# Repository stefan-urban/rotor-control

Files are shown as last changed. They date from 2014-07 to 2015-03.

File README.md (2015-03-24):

Rotor control with BeagleBone Black
===================================

Dieses Projekt entstand als Teil meiner Bachelorarbeit. Es zielt darauf ab ein Interface für zwei Antennenrotoren (unterschiedlicher Hersteller) zu bauen. Dieses soll eine Schnittstelle zu hamlib besitzen.



Vorraussetzungen
----------------

Hardware
- BeagleBone Black (=BBB)
- Cape wie unter dem Ordner `/hardware/eagle-project`
- Rotoren:
 - Create ERC5A (Elevation)
 - Yaesu G-2800DXC (Azimuth)

Software
- Debian 7.x mit
 - libpcre3-dev
 - libconfig-dev
 - libhamlib-utils (beinhaltet rotctl, rotctld)
- Auf dem Host-PC
 - Gpredict

Installation & Inbetriebnahme
-----------------------------

1. Software (unter `/software/`) aus diesem Repository in beliebigen Ordner auf dem BBB speichern.

2. (Optional) Konfigurationsfile unter `/etc/rotor_control.conf` anlegen. Eine Beispielkonfiguration ist im Ornder `docs` beigelegt.

3. (Optional) Rsyslogd konfigurieren.

 Standardmäßig werden alle Logging-Meldungen in `/var/log/syslog` mit allen anderen Meldungen vom System vermischt. Wie unser Programm ein eigene Logging-Datei erhält wird im beiliegenen Dokument [syslog.md](docs/syslog.md) erklärt.

5. Installieren
 ```
 debian@beaglebone:~/code/rotor-control/software$ sudo ./scripts/install.sh
 ```

 Jetzt werden alle erforderlichen Dateien in die entsprechenden Verzeichnise kopiert:
 - Programm und Start/Stop-Skripte nach `/opt/rotor-control/`
 - Daemon nach `/etc/init.d/`

6. Dienst starten
 ```
 debian@beaglebone:~/code/rotor-control/software$ sudo service rotor-control start
 ```

8. Verbindung mit gPredict aufbauen

 8.1. Gpredict starten
 
 8.2. Unter _Bearbeiten_ > _Einstellungen_ > _Interfaces_ > _Rotators_ einen neuen Rotor hinzufügen.
 
 8.3 Im Hauptfenster rechts oben auf den nach unten zeigenden Pfeil drücken und im erscheinenen Menü _Antennenkontrolle_ auswählen
 
 8.4 Es erscheint folgendes Fenster:

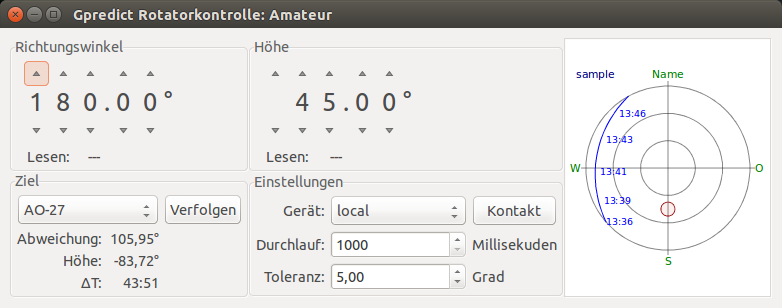
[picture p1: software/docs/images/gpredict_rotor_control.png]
gpredict_rotor_control
 
 
 8.5 Mit Drücken von _Kontakt_ wird die Verbindung zum BBB hergestellt und versucht die eingestellt Position anzufahren.

Verwendung ohne Rotoren
-----------------------

Zum Debugging ist es oft hilfreich das Programm __ohne__ die Rotorenanbindung zu betreiben. Dies ist möglich wenn in der Konfiguration die Simulation eingeschaltet wird. Dann wie oben beschrieben vorgehen.

Hintergrund: Als Rotorenansteuerung kommen jetzt nicht diverse GPIOs und ADCs zum Einsatz, welche es auf PCs gar nicht gibt, sondern ein Simulator.

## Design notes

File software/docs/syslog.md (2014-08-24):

Logging mit Rsyslog
==================

Das Logging wird mit Rsyslog, welches bereits auf der bestehenden Debian-Platform vorhanden ist, realisiert.

In der Standardeinstellung werden alle Meldungen von Rsyslog in `/var/log/syslog` gespeichert. Ist es gewünscht für die Rotorsteuerung ein eigenes Logfile zu erstellen, muss dies in der Konfiguration von Rsyslog geändert werden. Hierzu erstellt man eine neue Datei unter `/etc/rsyslog.d/` und fügt folgenden Text ein:

```
if $programname == 'rotor_control' then /var/log/rotor_control.log
```

Anschließend muss Rsyslog noch neu gestartet werden:

```
service rsyslog restart
```

Ab sofort findet man alle Logfile-Einträge unserer Anwendung unter `/var/log/rotor_control.log`.

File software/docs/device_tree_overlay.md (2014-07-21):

Device Tree Overlay
===================

All sources for the dto files already included in the default Debian distribution can be found here:
```
https://github.com/beagleboard/devicetree-source/tree/master/arch/arm/boot/dts
```

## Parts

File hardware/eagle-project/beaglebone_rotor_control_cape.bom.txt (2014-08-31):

Stückliste exportiert aus /home/stefan/Repositories/rotor-control/hardware/eagle-project/beaglebone_rotor_control_cape.sch am 31.08.14 10:45

Part Value              Device             Package           Description                                      
C1   100n               C-EUC0603          C0603             CAPACITOR, European symbol                       
C2   100n               C-EUC0603          C0603             CAPACITOR, European symbol                       
C3   100n               C-EUC0603          C0603             CAPACITOR, European symbol                       
C4   100n               C-EUC0603          C0603             CAPACITOR, European symbol                       
C5   100n               C-EUC0603          C0603             CAPACITOR, European symbol                       
C6   100n               C-EUC0603          C0603             CAPACITOR, European symbol                       
C7   100n               C-EUC0603          C0603             CAPACITOR, European symbol                       
C8   100n               C-EUC0603          C0603             CAPACITOR, European symbol                       
C9   100n               C-EUC0603          C0603             CAPACITOR, European symbol                       
C10  100n               C-EUC0603          C0603             CAPACITOR, European symbol                       
D1   BAS40-04           BAS40-04           SOT23             Silicon Schottky Diodes                          
D2   5V1                ZENER-DIODESOT23   SOT23             Z-Diode                                          
D3   BAS40-04           BAS40-04           SOT23             Silicon Schottky Diodes                          
D4   5V1                ZENER-DIODESOT23   SOT23             Z-Diode                                          
IC1  TLC2264CDU         TLC2264CDU         SO14              Quad Operational Amplifier                       
IC2  MCP4901            MCP4901            SO-08             8-Bit Voltage Output                             
IC3  MAX3232ESE         MAX3232ESE         SO16              True RS-232 Transceivers 3.0V to 5.5V, Low-Power 
IC6  TLC2264CDU         TLC2264CDU         SO14              Quad Operational Amplifier                       
Q1   SQ2348ES-T1-GE3    SQ2348ES-T1-GE3    SOT23             Automotive N-Channel MOSFET                      
Q2   SQ2348ES-T1-GE3    SQ2348ES-T1-GE3    SOT23             Automotive N-Channel MOSFET                      
Q3   SQ2348ES-T1-GE3    SQ2348ES-T1-GE3    SOT23             Automotive N-Channel MOSFET                      
Q4   SQ2348ES-T1-GE3    SQ2348ES-T1-GE3    SOT23             Automotive N-Channel MOSFET                      
Q5   SQ2348ES-T1-GE3    SQ2348ES-T1-GE3    SOT23             Automotive N-Channel MOSFET                      
Q6   SQ2348ES-T1-GE3    SQ2348ES-T1-GE3    SOT23             Automotive N-Channel MOSFET                      
R1   100                R-EU_R0805         R0805             RESISTOR, European symbol                        
R2   1M                 R-EU_R0805         R0805             RESISTOR, European symbol                        
R3   1M                 R-EU_R0805         R0805             RESISTOR, European symbol                        
R4   10k                R-EU_R0805         R0805             RESISTOR, European symbol                        
R5   5k6                R-EU_R0805         R0805             RESISTOR, European symbol                        
R6   100                R-EU_R0805         R0805             RESISTOR, European symbol                        
R7   100                R-EU_R0805         R0805             RESISTOR, European symbol                        
R8   100                R-EU_R0805         R0805             RESISTOR, European symbol                        
R9   100                R-EU_R0805         R0805             RESISTOR, European symbol                        
R10  10k                R-EU_R0805         R0805             RESISTOR, European symbol                        
R11  0                  R-EU_R0805         R0805             RESISTOR, European symbol                        
R12  5k                 R-EU_R0805         R0805             RESISTOR, European symbol                        
R13  10k                R-EU_R0805         R0805             RESISTOR, European symbol                        
R18  100                R-EU_R0805         R0805             RESISTOR, European symbol                        
R19  100                R-EU_R0805         R0805             RESISTOR, European symbol                        
R20  100                R-EU_R0805         R0805             RESISTOR, European symbol                        
R26  10k                R-EU_R0805         R0805             RESISTOR, European symbol                        
R27  5k6                R-EU_R0805         R0805             RESISTOR, European symbol                        
R28  10k                R-EU_R0805         R0805             RESISTOR, European symbol                        
R29  1M                 R-EU_R0805         R0805             RESISTOR, European symbol                        
R30  1M                 R-EU_R0805         R0805             RESISTOR, European symbol                        
R31  100                R-EU_R0805         R0805             RESISTOR, European symbol                        
R32  100                R-EU_R0805         R0805             RESISTOR, European symbol                        
R33  1M                 R-EU_R0805         R0805             RESISTOR, European symbol                        
R34  100                R-EU_R0805         R0805             RESISTOR, European symbol                        
R35  1M                 R-EU_R0805         R0805             RESISTOR, European symbol                        
R36  100                R-EU_R0805         R0805             RESISTOR, European symbol                        
R37  10k                R-EU_R0805         R0805             RESISTOR, European symbol                        
R38  10k                R-EU_R0805         R0805             RESISTOR, European symbol                        
R39  10k                R-EU_R0805         R0805             RESISTOR, European symbol                        
R40  10k                R-EU_R0805         R0805             RESISTOR, European symbol                        
U1   TMH0512S           TMH0512S           SIP               DC/DC Converter - TMH Series, 2 Watt             
X1   BEAGLEBONE_OUTLINE BEAGLEBONE_OUTLINE BEAGLEBONE_SHIELD BeagleBone Black Reference Layout                
X2                      F09VP              F09VP             SUB-D                                            
X4   DSUB9              DSUB9              DSUB9             3-1634222-2                                      
X5   USBDEV             USBDEV             USB               USB Buchse - Typ A, abgewinkelt

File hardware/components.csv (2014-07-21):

IC Samples
Manufacturer | Partnumber | Quantity | Package | Description
Vishay | SQ2348ES-T1-GE3 | 25 | SOT-23 | Automotive N-Channel 30 V (D-S) 175 °C MOSFET
TI | MAX232ID | 3 | SOIC-16 | Dual EIA-232 Driver/Receiver
TI | TLC2264CN | 3 | DIP-14 | Quad Rail-to-Rail OpAmp
TI | TLC2264CD | 3 | SOIC-14 | Quad Rail-to-Rail OpAmp
TI | TLV5616CP | 3 | DIP-8 | 12-bit DAC, SPI
TI | SN65HVD1782DR | 3 | SOIC-8 | RS485 Driver/Receiver, Fault-Prot.
TI | TPL0501-100DCNR | 3 | SOT-23/8 | Digital Potentiometer
TI | ADS1110A0IDBVT | 3 | SOT-23/6 | 16-bit self-calib. ADC
TI | REF3233AIDBVTG4 | 3 | SOT-23/6 | LDO Voltage-Reference 3.3V
TI | MAX232IN | 3 | DIP-16 | Dual EIA-232 Driver/Receiver
TI | SN65HVD30DR | 3 | SOIC-8 | RS485 Driver/Receiver, 3.3V
Microchip | MCP4901 | 3 | DIP-8 | DAC, SPI, 8-bit
Microchip | MCP4901 | 3 | SOIC-8 | DAC, SPI, 8-bit
MAXIM | MAX3232ESE+ | 10 | Narrow SO-16 | RS232 DRV/RCV, 3.3V compliant
Vishay | BAS40-04-HE3-08 | 15 | SOT-23 | Dual schottky diode, serial
MAXIM | MAX3232EPE+ | 5 | DIP-16 | RS232 DRV/RCV, 3.3V compliant
TI | TLV5616CDR | 3 | SOIC-8 | 12-Bit, 3 us DAC, Serial Input
TI | TLC2264CD | 3 | SOIC-14 | Quad Rail-to-Rail OpAmp
TI | SN65HVD78DR | 3 | SOIC-8 | TXRX RS485 3.3V ESD

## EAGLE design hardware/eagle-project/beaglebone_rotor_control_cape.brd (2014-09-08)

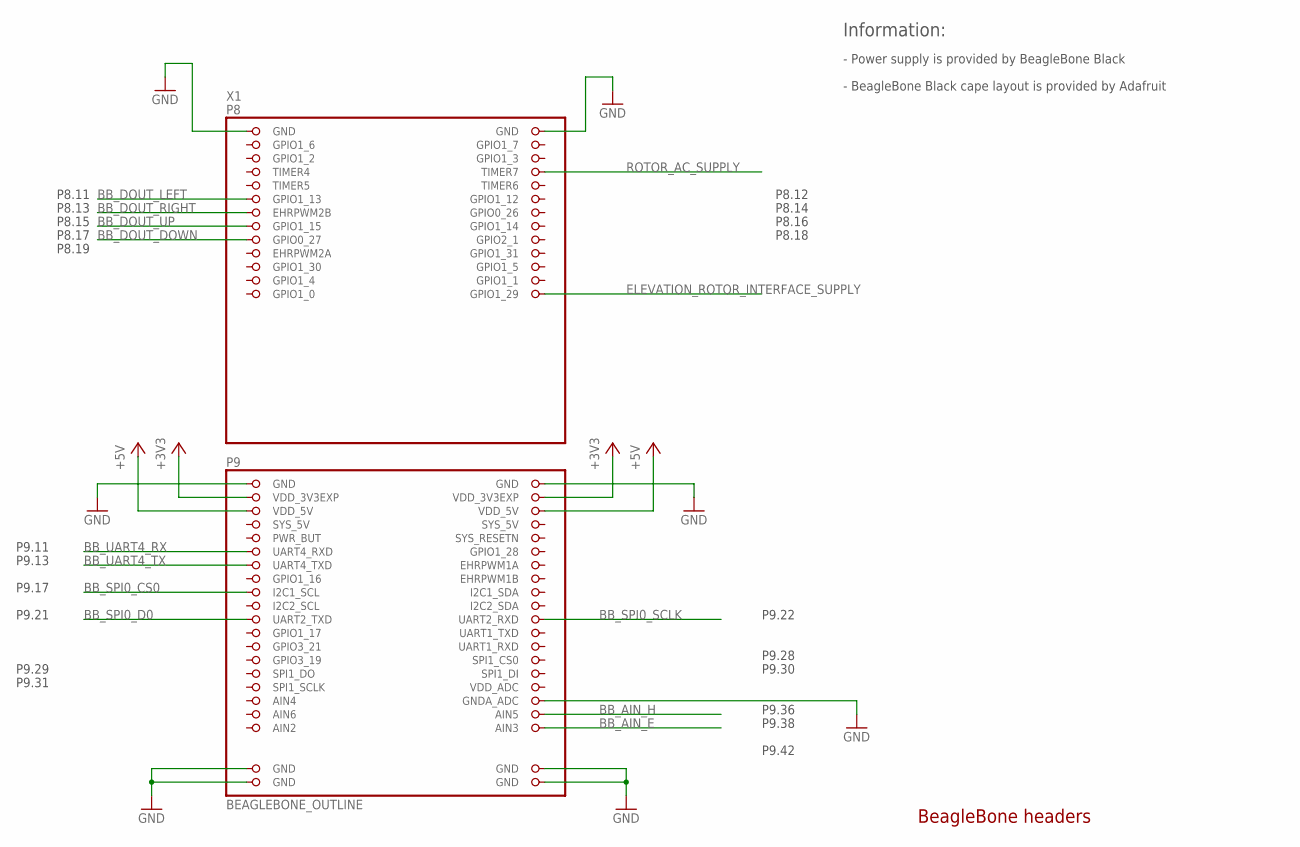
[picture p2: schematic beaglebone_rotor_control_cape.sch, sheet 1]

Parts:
X1: BEAGLEBONE_OUTLINE; BEAGLEBONE_SHIELD

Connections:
+3V3: X1.49 (VDD_3V3EXP), X1.50 (VDD_3V3EXP); also elsewhere on the board
+5V: X1.51 (VDD_5V), X1.52 (VDD_5V); also elsewhere on the board
BB_AIN_E: X1.84 (AIN3); also elsewhere on the board
BB_AIN_H: X1.82 (AIN5); also elsewhere on the board
BB_DOUT_DOWN: X1.17 (GPIO0_27); also elsewhere on the board
BB_DOUT_LEFT: X1.11 (GPIO1_13); also elsewhere on the board
BB_DOUT_RIGHT: X1.13 (EHRPWM2B); also elsewhere on the board
BB_DOUT_UP: X1.15 (GPIO1_15); also elsewhere on the board
BB_SPI0_CS0: X1.63 (I2C1_SCL); also elsewhere on the board
BB_SPI0_D0: X1.67 (UART2_TXD); also elsewhere on the board
BB_SPI0_SCLK: X1.68 (UART2_RXD); also elsewhere on the board
BB_UART4_RX: X1.57 (UART4_RXD); also elsewhere on the board
BB_UART4_TX: X1.59 (UART4_TXD); also elsewhere on the board
ELEVATION_ROTOR_INTERFACE_SUPPLY: X1.26 (GPIO1_29); also elsewhere on the board
GND: X1.1 (GND), X1.2 (GND), X1.47 (GND), X1.48 (GND), X1.80 (GNDA_ADC), X1.89 (GND), X1.90 (GND), X1.91 (GND), X1.92 (GND); also elsewhere on the board
ROTOR_AC_SUPPLY: X1.8 (TIMER7); also elsewhere on the board
SYS_5V: X1.53 (SYS_5V)

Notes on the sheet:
BeagleBone headers
- Power supply is provided by BeagleBone Black
Information:
- BeagleBone Black cape layout is provided by Adafruit
P9.17
P9.22
P9.21
P9.13
P9.11
P9.29
P9.30
P9.31
P9.28
P8.11
P8.13
P8.15
P8.17
P8.19
P8.12
P8.14
P8.16
P8.18
P9.36
P9.38
P9.42

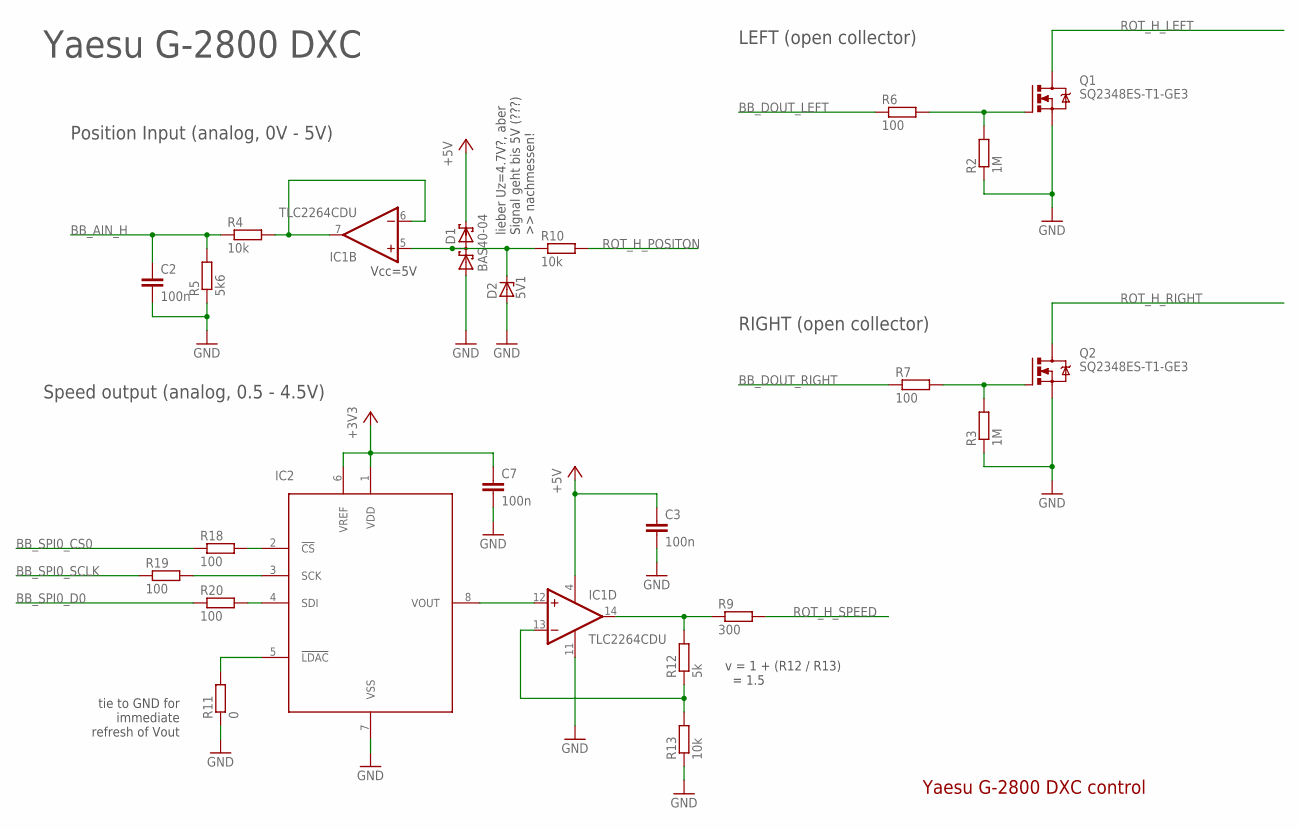
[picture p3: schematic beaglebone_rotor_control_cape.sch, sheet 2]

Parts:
C2, C3, C7: 100n; C0603
D1: BAS40-04; SOT23
D2: 5V1; SOT23
IC1: TLC2264CDU; SO14
IC2: MCP4901; SO-08
Q1, Q2: SQ2348ES-T1-GE3; SOT23
R2, R3: 1M; R0805
R4, R10, R13: 10k; R0805
R5: 5k6; R0805
R6, R7, R18, R19, R20: 100; R0805
R9: 300; R0805
R11: 0; R0805
R12: 5k; R0805

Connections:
+3V3: C7.1, IC2.1 (VDD), IC2.6 (VREF); also elsewhere on the board
+5V: C3.1, D1.2 (C2), IC1.4 (V+); also elsewhere on the board
BB_AIN_H: C2.1, R4.1, R5.2; also elsewhere on the board
BB_DOUT_LEFT: R6.1; also elsewhere on the board
BB_DOUT_RIGHT: R7.1; also elsewhere on the board
BB_SPI0_CS0: R18.1; also elsewhere on the board
BB_SPI0_D0: R20.1; also elsewhere on the board
BB_SPI0_SCLK: R19.1; also elsewhere on the board
GND: C2.2, C3.2, C7.2, D1.1 (A1), D2.1 (A), IC1.11 (V-), IC2.7 (VSS), Q1.2 (S), Q2.2 (S), R2.1, R3.1, R5.1, R11.1, R13.1; also elsewhere on the board
unnamed: IC1.6 (-IN), IC1.7 (OUT), R4.2
unnamed: IC1.12 (+IN), IC2.8 (VOUT)
unnamed: IC1.14 (OUT), R9.1, R12.2
unnamed: IC1.13 (-IN), R12.1, R13.2
unnamed: IC2.2 (!CS), R18.2
unnamed: IC2.5 (!LDAC), R11.2
unnamed: IC2.4 (SDI), R20.2
unnamed: IC2.3 (SCK), R19.2
unnamed: Q2.1 (G), R3.2, R7.2
unnamed: D1.3 (C1A2), D2.3 (C), IC1.5 (+IN), R10.1
unnamed: Q1.1 (G), R2.2, R6.2
ROT_H_LEFT: Q1.3 (D); also elsewhere on the board
ROT_H_POSITON: R10.2; also elsewhere on the board
ROT_H_RIGHT: Q2.3 (D); also elsewhere on the board
ROT_H_SPEED: R9.2; also elsewhere on the board

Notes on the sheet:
Yaesu G-2800 DXC control
LEFT (open collector)
RIGHT (open collector)
Position Input (analog, 0V - 5V)
Yaesu G-2800 DXC
Speed output (analog, 0.5 - 4.5V)
lieber Uz=4.7V?, aber Signal geht bis 5V (???) >> nachmessen!
Vcc=5V
tie to GND for immediate refresh of Vout
v = 1 + (R12 / R13) = 1.5

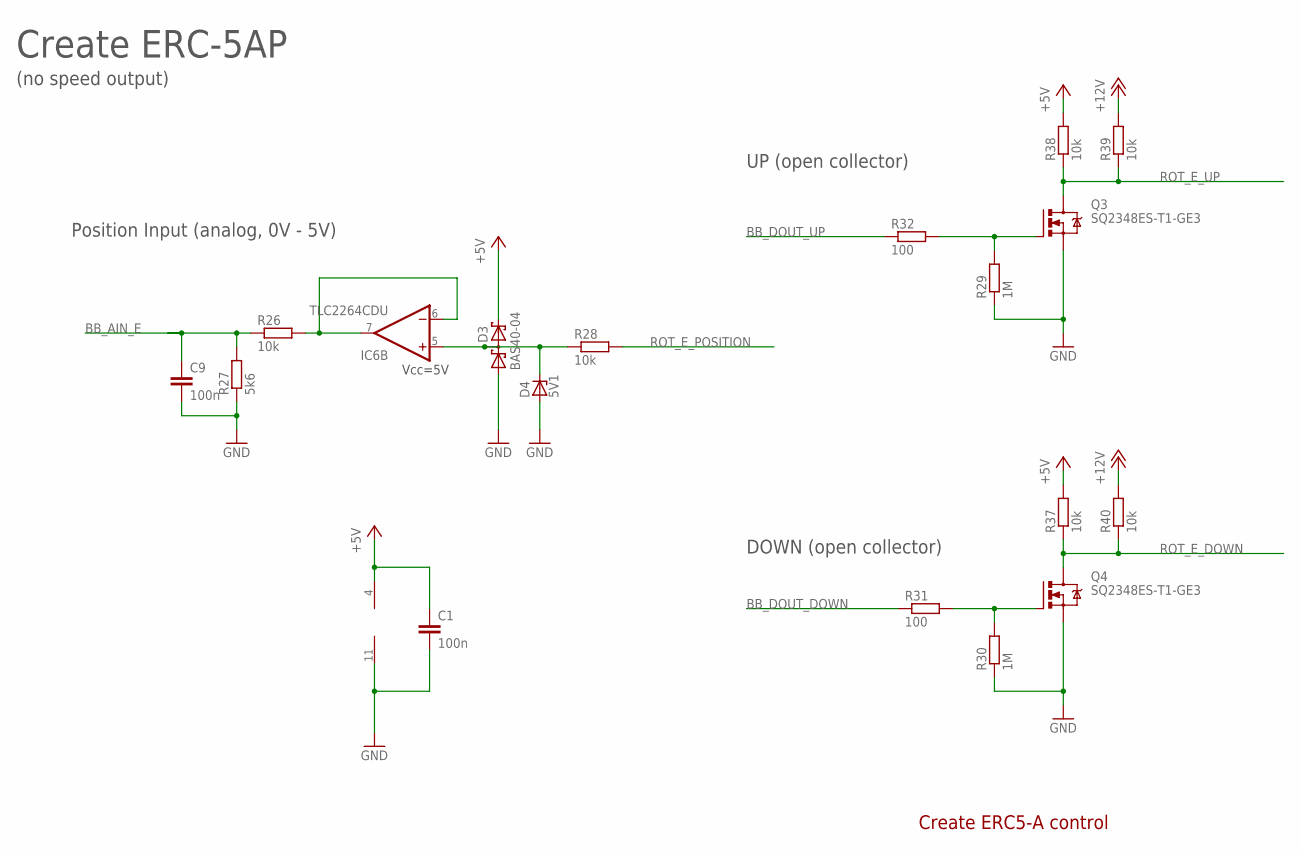
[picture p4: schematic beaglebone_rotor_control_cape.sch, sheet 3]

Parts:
C1, C9: 100n; C0603
D3: BAS40-04; SOT23
D4: 5V1; SOT23
IC6: TLC2264CDU; SO14
Q3, Q4: SQ2348ES-T1-GE3; SOT23
R26, R28, R37, R38, R39, R40: 10k; R0805
R27: 5k6; R0805
R29, R30: 1M; R0805
R31, R32: 100; R0805

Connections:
+5V: C1.1, D3.2 (C2), IC6.4 (V+), R37.2, R38.2; also elsewhere on the board
+12V: R39.2, R40.2; also elsewhere on the board
BB_AIN_E: C9.1, R26.1, R27.2; also elsewhere on the board
BB_DOUT_DOWN: R31.1; also elsewhere on the board
BB_DOUT_UP: R32.1; also elsewhere on the board
GND: C1.2, C9.2, D3.1 (A1), D4.1 (A), IC6.11 (V-), Q3.2 (S), Q4.2 (S), R27.1, R29.1, R30.1; also elsewhere on the board
unnamed: IC6.6 (-IN), IC6.7 (OUT), R26.2
unnamed: D3.3 (C1A2), D4.3 (C), IC6.5 (+IN), R28.1
unnamed: Q3.1 (G), R29.2, R32.2
unnamed: Q4.1 (G), R30.2, R31.2
ROT_E_DOWN: Q4.3 (D), R37.1, R40.1; also elsewhere on the board
ROT_E_POSITION: R28.2; also elsewhere on the board
ROT_E_UP: Q3.3 (D), R38.1, R39.1; also elsewhere on the board

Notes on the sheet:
Create ERC5-A control
Position Input (analog, 0V - 5V)
Vcc=5V
Create ERC-5AP
UP (open collector)
DOWN (open collector)
(no speed output)

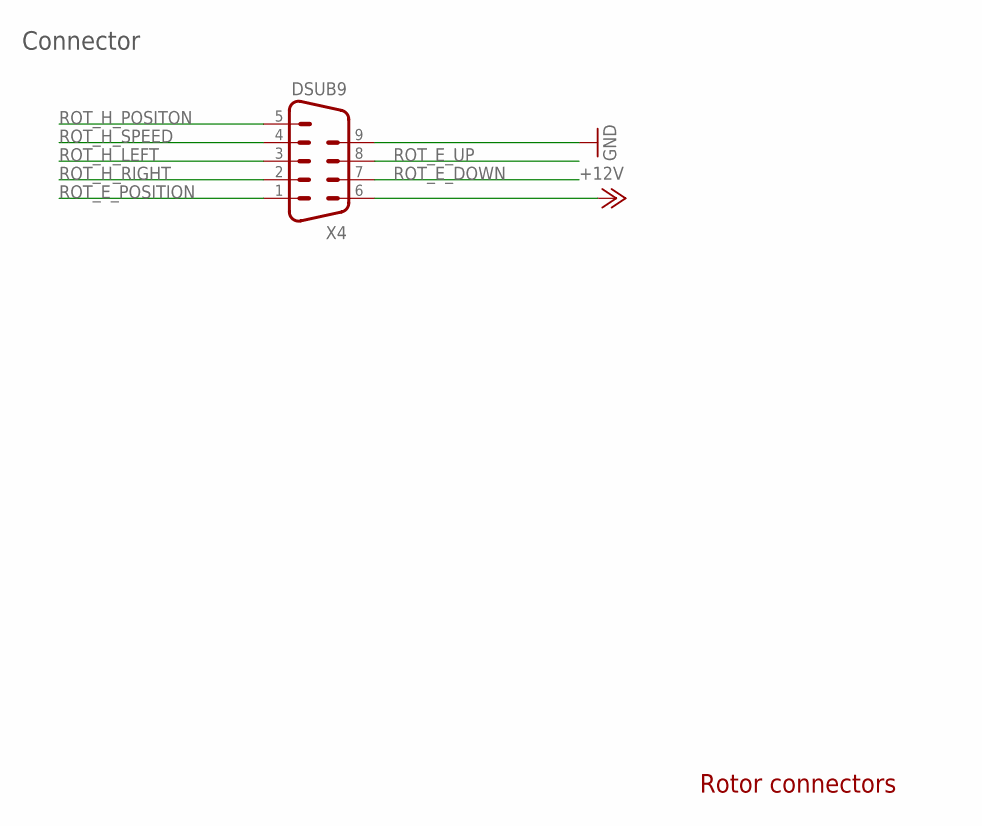
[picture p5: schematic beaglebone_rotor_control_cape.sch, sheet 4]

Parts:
X4: DSUB9

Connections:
+12V: X4.6; also elsewhere on the board
GND: X4.9; also elsewhere on the board
ROT_E_DOWN: X4.7; also elsewhere on the board
ROT_E_POSITION: X4.1; also elsewhere on the board
ROT_E_UP: X4.8; also elsewhere on the board
ROT_H_LEFT: X4.3; also elsewhere on the board
ROT_H_POSITON: X4.5; also elsewhere on the board
ROT_H_RIGHT: X4.2; also elsewhere on the board
ROT_H_SPEED: X4.4; also elsewhere on the board

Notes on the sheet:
Rotor connectors
Connector

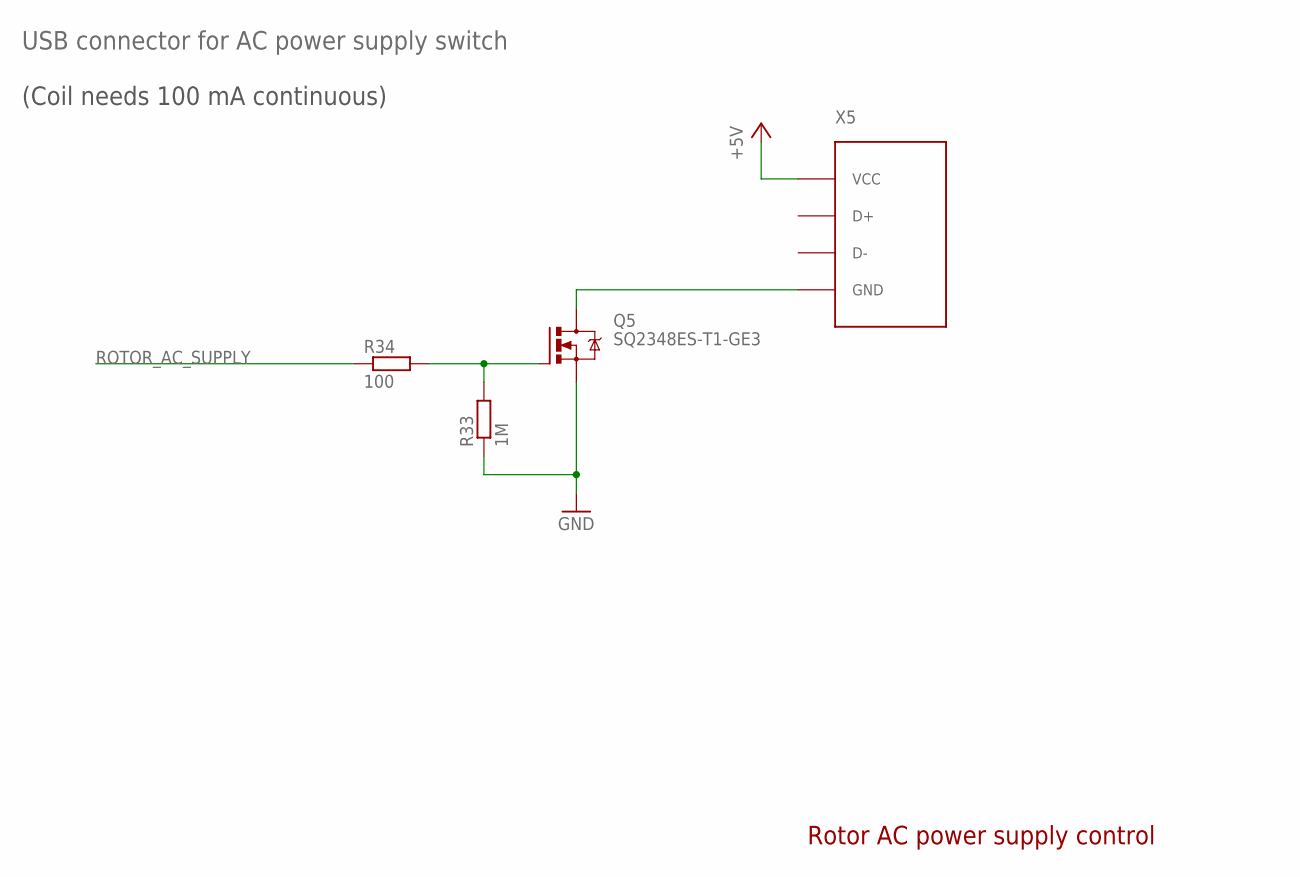
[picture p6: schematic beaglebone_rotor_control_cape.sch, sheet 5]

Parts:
Q5: SQ2348ES-T1-GE3; SOT23
R33: 1M; R0805
R34: 100; R0805
X5: USBDEV; USB

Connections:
+5V: X5.1-VCC (VCC); also elsewhere on the board
GND: Q5.2 (S), R33.1; also elsewhere on the board
unnamed: Q5.3 (D), X5.GND
unnamed: Q5.1 (G), R33.2, R34.2
ROTOR_AC_SUPPLY: R34.1; also elsewhere on the board

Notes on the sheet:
Rotor AC power supply control
USB connector for AC power supply switch
(Coil needs 100 mA continuous)

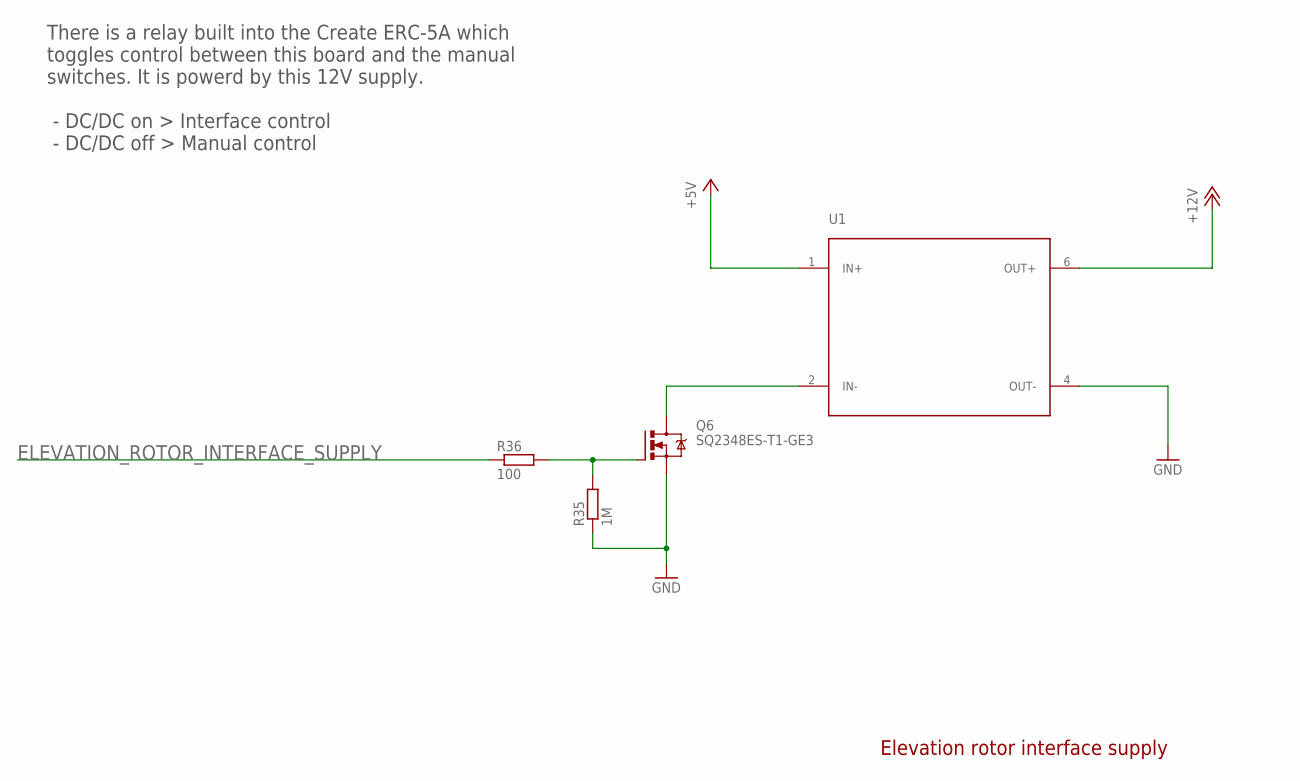
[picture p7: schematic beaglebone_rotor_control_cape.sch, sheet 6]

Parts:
Q6: SQ2348ES-T1-GE3; SOT23
R35: 1M; R0805
R36: 100; R0805
U1: TMH0512S; SIP

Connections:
+5V: U1.1 (IN+); also elsewhere on the board
+12V: U1.6 (OUT+); also elsewhere on the board
ELEVATION_ROTOR_INTERFACE_SUPPLY: R36.1; also elsewhere on the board
GND: Q6.2 (S), R35.1, U1.4 (OUT-); also elsewhere on the board
unnamed: Q6.1 (G), R35.2, R36.2
unnamed: Q6.3 (D), U1.2 (IN-)

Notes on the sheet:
Elevation rotor interface supply
There is a relay built into the Create ERC-5A which toggles control between this board and the manual switches. It is powerd by this 12V supply. - DC/DC on > Interface control - DC/DC off > Manual control

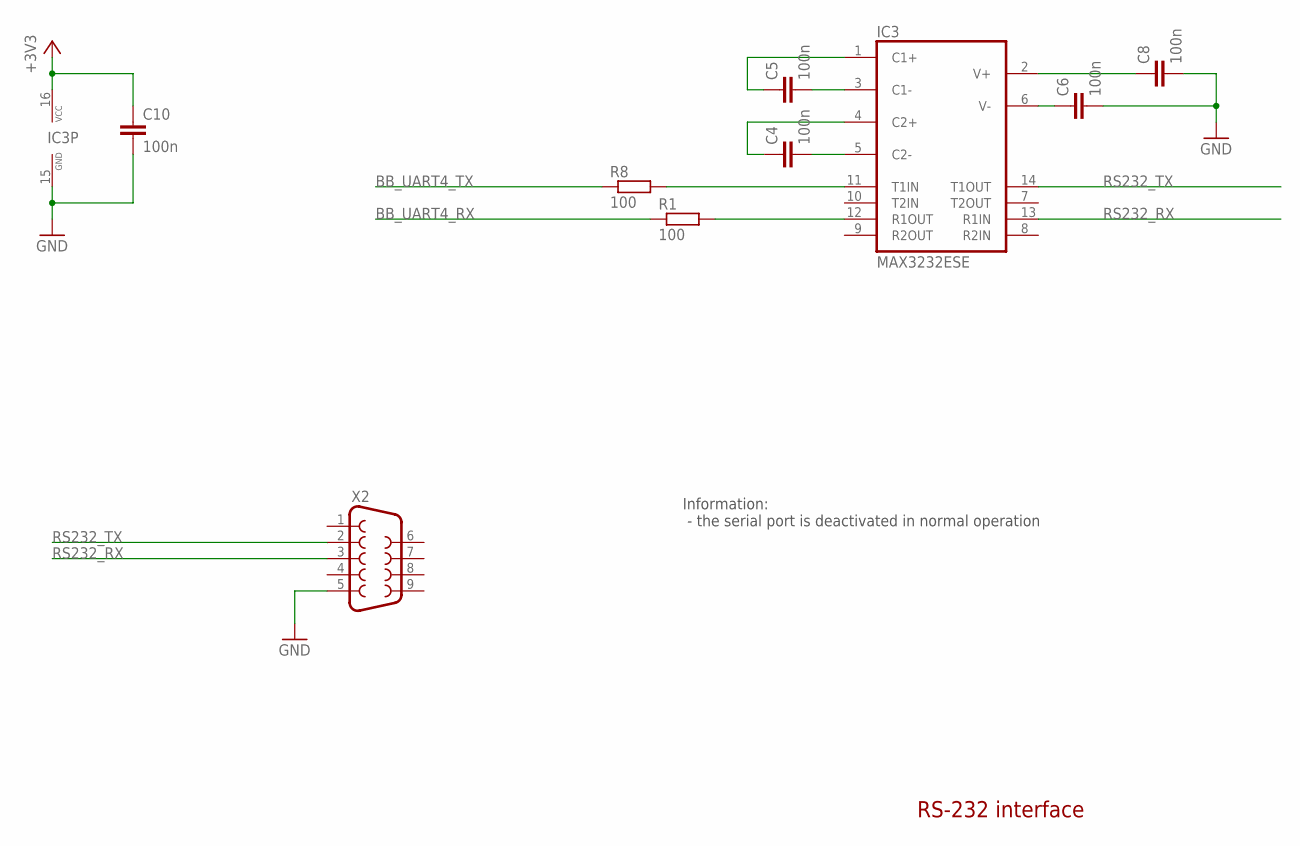
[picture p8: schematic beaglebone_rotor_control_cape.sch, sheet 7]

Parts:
C4, C5, C6, C8, C10: 100n; C0603
IC3: MAX3232ESE; SO16
R1, R8: 100; R0805
X2: F09VP

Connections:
+3V3: C10.1, IC3.16 (VCC); also elsewhere on the board
BB_UART4_RX: R1.1; also elsewhere on the board
BB_UART4_TX: R8.1; also elsewhere on the board
GND: C6.2, C8.2, C10.2, IC3.15 (GND), X2.5; also elsewhere on the board
unnamed: C4.1, IC3.4 (C2+)
unnamed: C4.2, IC3.5 (C2-)
unnamed: C5.2, IC3.3 (C1-)
unnamed: C5.1, IC3.1 (C1+)
unnamed: C6.1, IC3.6 (V-)
unnamed: C8.1, IC3.2 (V+)
unnamed: IC3.11 (T1IN), R8.2
unnamed: IC3.12 (R1OUT), R1.2
RS232_RX: IC3.13 (R1IN), X2.3
RS232_TX: IC3.14 (T1OUT), X2.2

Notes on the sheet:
RS-232 interface
Information: - the serial port is deactivated in normal operation

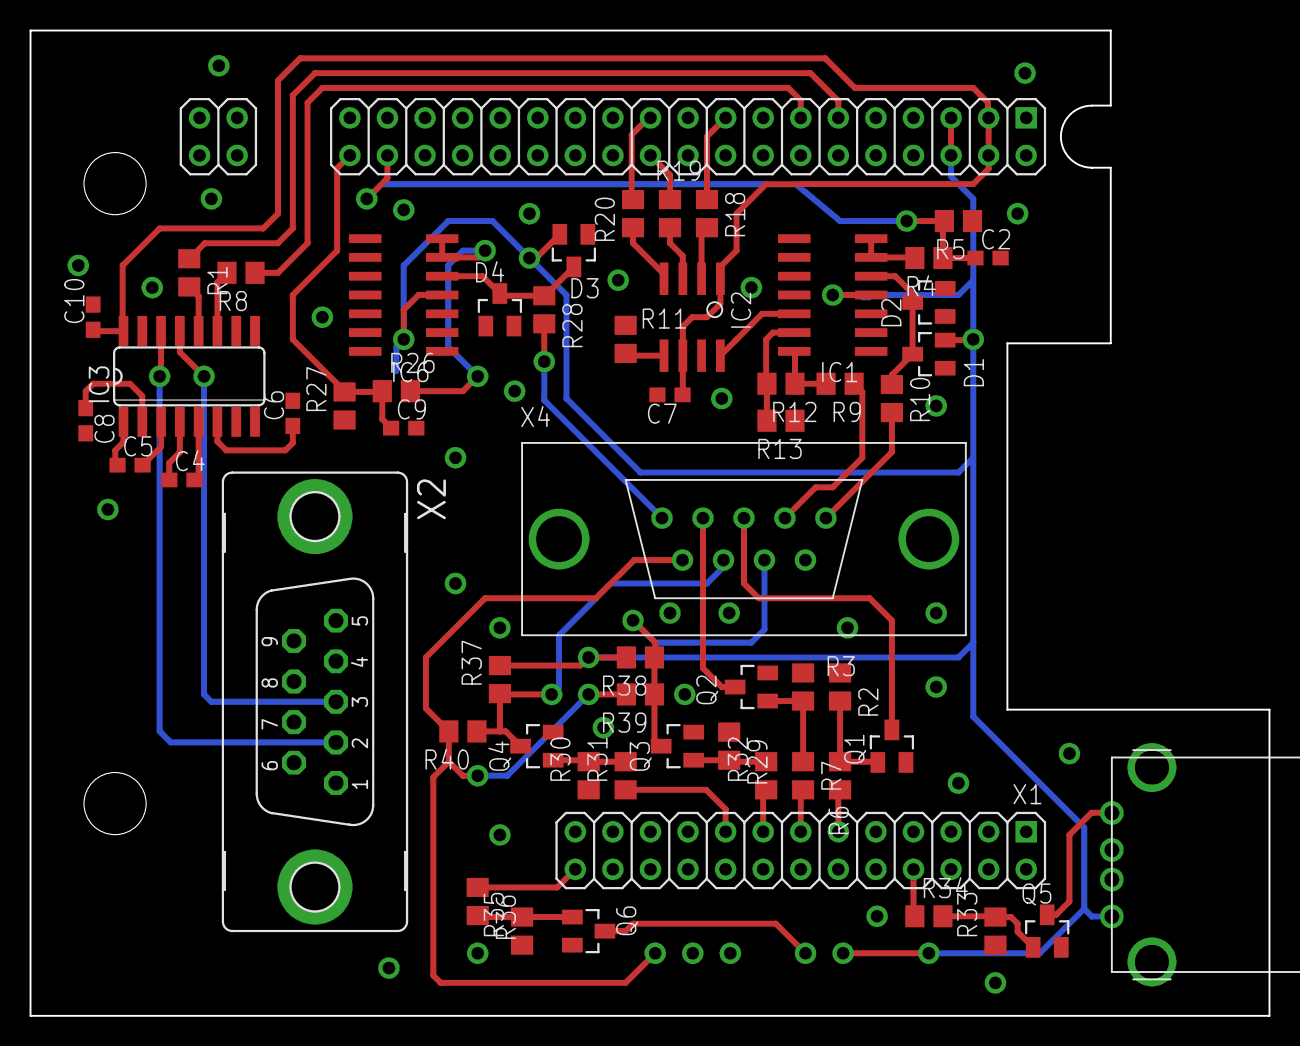
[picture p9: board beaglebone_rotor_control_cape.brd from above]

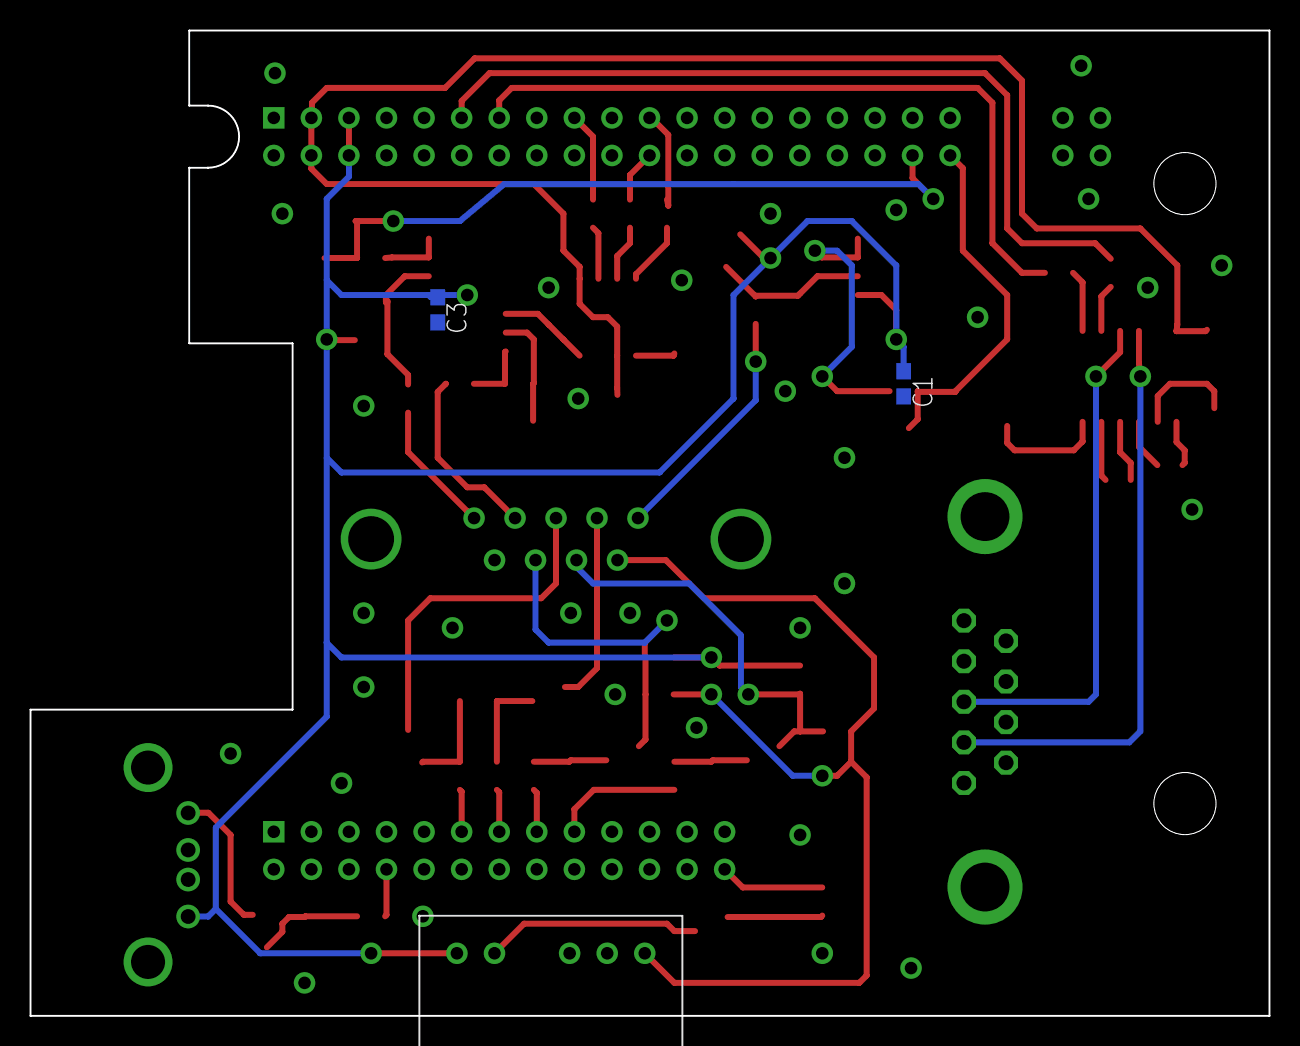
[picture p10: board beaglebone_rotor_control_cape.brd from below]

Board: 2 copper layers, 83.8 x 66.6 mm, 60 parts (3 on the bottom side), 53 nets.

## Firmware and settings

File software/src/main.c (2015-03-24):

/*
 * main.c
 *
 *  Created on: 26.05.2014
 *      Author: Stefan Urban <stefan.urban@live.de>
 *
 *  Sources:
 *      - https://github.com/cymait/virtual-serial-port-example
 *      - http://www.tldp.org/HOWTO/text/Serial-Programming-HOWTO
 */


#include <string.h>
#include <stdio.h>
#include <stdlib.h>
#include <unistd.h>
#include <fcntl.h>
#include <signal.h>
#include <pthread.h>


#include "configuration.h"
#include "debug.h"
#include "gpio.h"
#include "gs232-interface.h"
#include "pseudoterminal.h"


#define PTS_SYMLINK_PATH ("/dev/")


volatile int global_stop = 0;
pthread_t pts_threads[MAX_PSEUDOTERMINAL];
char paths[MAX_PSEUDOTERMINAL][100];

void termination_handler (int signum)
{
	global_stop = 1;
}

void* pts_listerner(void* ptr)
{
	int stop = 0;
	char debug_str[100], dev_file[100];

	// Build symlink path
	sprintf(dev_file, "%s%s", PTS_SYMLINK_PATH, (char*) ptr);


	// Open terminal to listen from
	intptr_t f;
	pseudoterminal_t pts;

// @todo: listen_console reimplement

//	if (configuration_get_listen_console_enabled())
//	{
//		sprintf(debug_str, "Using terminal: %s", configuration_get_listen_console_path());
//		debug_msg(LOG_INFO, debug_str);
//
//		f = open(configuration_get_listen_console_path(), O_RDWR | O_NOCTTY);
//
//		if (f < 0)
//		{
//			sprintf(debug_str, "Could not open terminal: %s",configuration_get_listen_console_path());
//			debug_msg(LOG_INFO, debug_str);
//		}
//	}
//	else
//	{
		// Setup pseudoterminal
		pts = pts_open();

		if (pts.fd < 0) {
			debug_msg(LOG_ERR, "Could not open pseudoterminal");
			return ptr;
		}

		f = pts.fd;

		sprintf(debug_str, "Pseudoterminal is open at: %s", pts.name);
		debug_msg(LOG_INFO, debug_str);

		// Create symlink on pseudoterminal
		unlink(dev_file);

		if (symlink(pts.name, dev_file) < 0)
		{
			sprintf(debug_str, "Pseudoterminal symlink could not be created");
			debug_msg(LOG_INFO, debug_str);
		}
		else
		{
			sprintf(debug_str, "Pseudoterminal symlink created at: %s", dev_file);
			debug_msg(LOG_INFO, debug_str);
		}
//	}


	// Read line by line from serial port
	char buffer[255], *ret_str;
	ssize_t size;

	while (stop == 0 &&  global_stop == 0)
	{
		// Read from serial port and make sure the string is terminated
		size = read (pts.fd, buffer, sizeof buffer);
		buffer[size] = '\0';

		sprintf(debug_str, "Did receive command: %s", buffer);
		debug_msg(LOG_INFO, debug_str);

		// Hand the command string over to the gs232 interface, which will interpret
		// the command and return a string to write back to the pts
		ret_str = gs232_command(buffer);

		sprintf(debug_str, "Answering: %s", ret_str);
		debug_msg(LOG_INFO, debug_str);

		// Write answer back to serial port
		size = strlen(ret_str);
		write(pts.fd, ret_str, size);

		// Quit
		if( buffer[0] == 'q' || global_stop == 1 )
		{
			debug_msg(LOG_NOTICE, "Quit command detected!");

			stop = 1;
		}

		usleep(10000);
	}


	if (configuration_get_listen_console_enabled() == 0)
	{
		pts_close(pts);

		unlink(dev_file);
	}
	else
	{
		close(f);
	}

	return ptr;
}

int main(int argc, char** argv) {

	// Setup right singal handling (allows to safely terminate applicaiton with Ctrl+C)
	// ... as described in http://www.gnu.org/software/libc/manual/html_node/Sigaction-Function-Example.html
	struct sigaction new_action, old_action;

	new_action.sa_handler = termination_handler;
	sigemptyset (&new_action.sa_mask);
	new_action.sa_flags = 0;

	sigaction (SIGINT, NULL, &old_action);
	if (old_action.sa_handler != SIG_IGN)
	{
		sigaction (SIGINT, &new_action, NULL);
	}

	sigaction (SIGKILL, NULL, &old_action);
	if (old_action.sa_handler != SIG_IGN)
	{
		sigaction (SIGKILL, &new_action, NULL);
	}

	sigaction (SIGTERM, NULL, &old_action);
	if (old_action.sa_handler != SIG_IGN)
	{
		sigaction (SIGTERM, &new_action, NULL);
	}


	char debug_str[100];

	debug_msg(LOG_NOTICE, "--------------------------------------------------");
	debug_msg(LOG_NOTICE, "Starting rotor_control!");

	configuration_init(argc, argv);
	gs232_init();


	int i;

	for (i = 0; i < configuration_get_pseudoterminals_num(); i++)
	{
		strcpy((paths[i]), configuration_get_pseudoterminal(i));

		sprintf(debug_str, "PTS create: %s%s", PTS_SYMLINK_PATH, paths[i]);
		debug_msg(LOG_INFO, debug_str);

		pthread_create(&(pts_threads[i]), NULL, &pts_listerner, paths[i]);
	}

	while (global_stop == 0)
	{
		// do nothing
	}

	gs232_destroy();

	debug_msg(LOG_NOTICE, "Shutting down now!");

	return 0;
}

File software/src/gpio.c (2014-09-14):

/*
 * gpio.c
 *
 *  Created on: 27.06.2014
 *      Author: Stefan Urban <stefan.urban@live.de>
 */

#include <stdio.h>
#include <stdlib.h>
#include <string.h>

#include "debug.h"


#define GPIO_BASE_PATH  "/sys/class/gpio/"

#define GPIO_EXPORT     GPIO_BASE_PATH "export"
#define GPIO_UNEXPORT   GPIO_BASE_PATH "unexport"

#define GPIO_DIRECTION  GPIO_BASE_PATH "gpio%d/direction"
#define GPIO_VALUE      GPIO_BASE_PATH "gpio%d/value"


int gpio_export(int pin)
{
	char debug_str[100];

	sprintf(debug_str, "GPIO: Export pin %d", pin);
	debug_msg(LOG_DEBUG, debug_str);


	FILE *fp = NULL;

	if ((fp = fopen(GPIO_EXPORT, "w")) == NULL)
	{
			sprintf(debug_str, "GPIO: Could not export pin %d. Export file not found!", pin);
			debug_msg(LOG_ERR, debug_str);
		return -1;
	}

	fprintf(fp, "%d", pin);
	fclose(fp);

	// Set direction to out
	char gpio_direction[50];

	sprintf(debug_str, "GPIO: Setting direction of pin %d to 'out'.", pin);
	debug_msg(LOG_DEBUG, debug_str);

	sprintf(gpio_direction, GPIO_DIRECTION, pin);

	if ((fp = fopen(gpio_direction, "w")) == NULL)
	{
		sprintf(debug_str, "GPIO: Setting direction failed %d", pin);
		debug_msg(LOG_ERR, debug_str);

		return -1;
	}

	fprintf(fp, "out");
	fclose(fp);

	return 0;
}

int gpio_unexport(int pin)
{
	char debug_str[100];

	sprintf(debug_str, "GPIO: Unexport pin %d", pin);
	debug_msg(LOG_DEBUG, debug_str);


	FILE *fp = NULL;

	if ((fp = fopen(GPIO_UNEXPORT, "w")) == NULL)
	{
		sprintf(debug_str, "GPIO: Could not unexport pin %d. Unexport file not found!", pin);
		debug_msg(LOG_DEBUG, debug_str);

		return -1;
	}

	fprintf(fp, "%d", pin);
	fclose(fp);

	return 0;
}

int gpio_set(int pin, int value)
{
	char debug_str[100];

	sprintf(debug_str, "GPIO: Set pin %d value to %d", pin, value);
	debug_msg(LOG_DEBUG, debug_str);


	FILE *fp = NULL;
	char gpio_value[50];

	sprintf(gpio_value, GPIO_VALUE, pin);

	if ((fp = fopen(gpio_value, "w")) == NULL)
	{
		sprintf(debug_str, "GPIO: Setting pin %d value failed. File does not exist!", pin);
		debug_msg(LOG_ERR, debug_str);

		return -1;
	}

	fprintf(fp, value ? "1" : "0");
	fclose(fp);

	return 0;
}

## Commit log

2014-05-15 Changed ADC channels to the ones on the PCB (was configured for breadboard setup)
2014-05-15 Tried to configure elevation position sensor, switch to real rotors
2014-05-15 Fixed debug messages for rotor moving direction (UP, DOWN, ...)
2014-05-15 Fixed error in command line parsing
    [main.c]
2014-05-15 Implemented ADC AIN5 & AIN6 for testing, reaction on 'Get position' command visible
2014-05-15 Created GPIOs according to Eagle schematic
2014-05-15 SPI communication implemented
2014-05-15 Changed GPIO numbers to the correct one, now works
    [gpio.c]
2014-05-26 main programm created, opens pseudo terminal and reads from it, not working good (wip, lunch break)
    [main.c]
2014-06-13 * added gs232 interface * problems with serial port, maybe problems with configuration?
    [main.c]
2014-06-20 Added eagle files (libraries, design rule check, schematics and layout)
    [beaglebone_rotor_control_cape.brd, beaglebone_rotor_control_cape.sch, components.csv]
2014-06-23 Eagle project update * RS232 rcv/drv layout done * AMP Press-Fit connector library created
    [beaglebone_rotor_control_cape.brd, beaglebone_rotor_control_cape.sch]
2014-06-23 Updated available components list
    [beaglebone_rotor_control_cape.brd, beaglebone_rotor_control_cape.sch, components.csv]
2014-06-24 New comments/thoughts in EAGLE schematics
    [beaglebone_rotor_control_cape.sch]
2014-06-24 Added specifications for TI TLV5616 in c-file chip may not be suitable for our application, maybe switch to Microchip MCP4901?
2014-06-24 Changed DAC from TI TLV5616 to Microchip MCP4901
    [beaglebone_rotor_control_cape.brd, beaglebone_rotor_control_cape.sch]
2014-06-24 Added software draft for MCP4901 and some Eagle schematic updates
    [beaglebone_rotor_control_cape.brd, beaglebone_rotor_control_cape.sch]
2014-06-26 Fixed break condition on main program
    [main.c]
2014-06-27 Hardware: Create ERC5-AP interface
    [beaglebone_rotor_control_cape.brd, beaglebone_rotor_control_cape.sch]
2014-06-27 Added link to device tree overlay sources
2014-07-21 Current GPIO usage in userspace is a fail
2014-07-24 * layout: added spi1 and determined pin for usb slave turn on
    [beaglebone_rotor_control_cape.brd, beaglebone_rotor_control_cape.sch]
2014-07-25 Fixed some strange merge errors
    [gpio.c, main.c]
2014-07-28 Created library for D-Sub connector from TE.com
    [beaglebone_rotor_control_cape.brd, beaglebone_rotor_control_cape.sch]
2014-07-28 Placed D-Sub connectors on layout
    [beaglebone_rotor_control_cape.brd, beaglebone_rotor_control_cape.sch]
2014-07-28 Added USB connector
    [beaglebone_rotor_control_cape.brd, beaglebone_rotor_control_cape.sch]
2014-07-29 Updated schematic
    [beaglebone_rotor_control_cape.brd, beaglebone_rotor_control_cape.sch]
2014-07-31 Updated eagle schematic
    [beaglebone_rotor_control_cape.brd, beaglebone_rotor_control_cape.sch]
2014-08-06 Added DCDC to eagle schematic and made first draft of layout
    [beaglebone_rotor_control_cape.brd, beaglebone_rotor_control_cape.sch]
2014-08-07 Improved Eagle layout, more free space on board for future components
    [beaglebone_rotor_control_cape.brd, beaglebone_rotor_control_cape.sch]
2014-08-11 Tweaked eagle layout for easier manufacturing
    [beaglebone_rotor_control_cape.brd]
2014-08-17 Optical tweaks for eagle schematic
    [beaglebone_rotor_control_cape.sch]
2014-08-17 Added serial interface chip to layout
    [beaglebone_rotor_control_cape.brd, beaglebone_rotor_control_cape.sch]
2014-08-18 Eagle layout update finalized for manufacturing
    [beaglebone_rotor_control_cape.brd, beaglebone_rotor_control_cape.sch]
2014-08-24 Implemented configuration file and command line options, fixed error in makefile
    [configuration.h]
2014-08-24 Refactored ADC function
2014-08-24 Code cleanup
    [configuration.h]
2014-08-25 Changed abstraction layers completely, added debug rotor for offline testing
2014-08-25 Minor fixes and cleanups
    [gpio.c]
2014-08-25 Debug rotor is now able to set position via 'Wxxx yyy' command.
2014-08-26 Rotors now support 'set position' command. Position sensor evaluation enhanced
    [configuration.h]
2014-08-26 Added configuration sample file
2014-08-28 Set position function of elevation rotor was not included in rotors struct
2014-08-31 Created BOM
    [beaglebone_rotor_control_cape.sch]
2014-08-31 Created schematic overview over power supply
    [stromversorgung_prinzip.sch]
2014-09-08 Changed short circuit protection resitor
    [beaglebone_rotor_control_cape.brd, beaglebone_rotor_control_cape.sch]
2014-09-08 Elevation rotor principle
    [elevationsrotor-prinzip.sch]
2014-09-13 Interpolation table support in master
    [configuration.h]
2014-09-13 Changed gray schematic color to black for better documentation readability
    [beaglebone_rotor_control_cape.sch, elevationsrotor-prinzip.sch, stromversorgung_prinzip.sch]
2014-09-14 Added missing configuration parameters
    [configuration.h]
2014-09-14 Added lots of commentation
    [configuration.h]
2014-09-14 New folder structure
    [configuration.h]
2014-09-14 Changed replys to ok and renamed executable to rotor-control
2014-09-14 Inserted measured values
2015-03-10 Fixed communication errors with multiple applications accessing rotor_control pts file
2015-03-24 Implementation of pseudoterminal configuration variable
    [configuration.h]
2015-03-24 Added support for multiple pseudoterminal creation, config file based
    [configuration.h]
